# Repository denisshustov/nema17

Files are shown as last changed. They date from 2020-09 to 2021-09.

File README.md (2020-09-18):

# nema17

<b>#3_2.ino - arduino scatch for ultrasonic sensors</b><br>
<br>
links:
https://www.intorobotics.com/how-to-use-sensor_msgs-range-ros-for-multiple-sensors-with-rosserial/<br>
http://cobecoballes-robotics.blogspot.com/2018/08/sonar-ranger-ros-rviz.html<br>
http://wiki.ros.org/rosserial_arduino/Tutorials/SRF08%20Ultrasonic%20Range%20Finder<br>

if add Kalman filter it works slow<br>
if send in different topics it works slow<br>

<b>RUN</b><br>
rosrun rosserial_python serial_node.py /dev/ttyUSB0<br>
rostopic echo /rangeSonar1<br>

#ultrasonic sensors problems<br>
if error like:<br>
~$ roslaunch turtlebot3_bringup turtlebot3_robot.launch <br>
... logging to /home/turtlebot3/.ros/log/50d0066c-1356-11e8-861b-a0c589238c19/roslaunch-turtlebot3-2515.log<br>
Checking log directory for disk usage. This may take awhile.<br>
Press Ctrl-C to interrupt<br>
Done checking log file disk usage. Usage is <1GB.<br>
<br>
<br>
Solution:<br>
change arduino with more RAM or cut code for arduino<br>

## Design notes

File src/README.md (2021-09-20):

# Vacuum cleaner operation by ROS

## Model
For desing use Fusion 360. For converting from Fusion 360 to urfd tool: https://github.com/syuntoku14/fusion2urdf

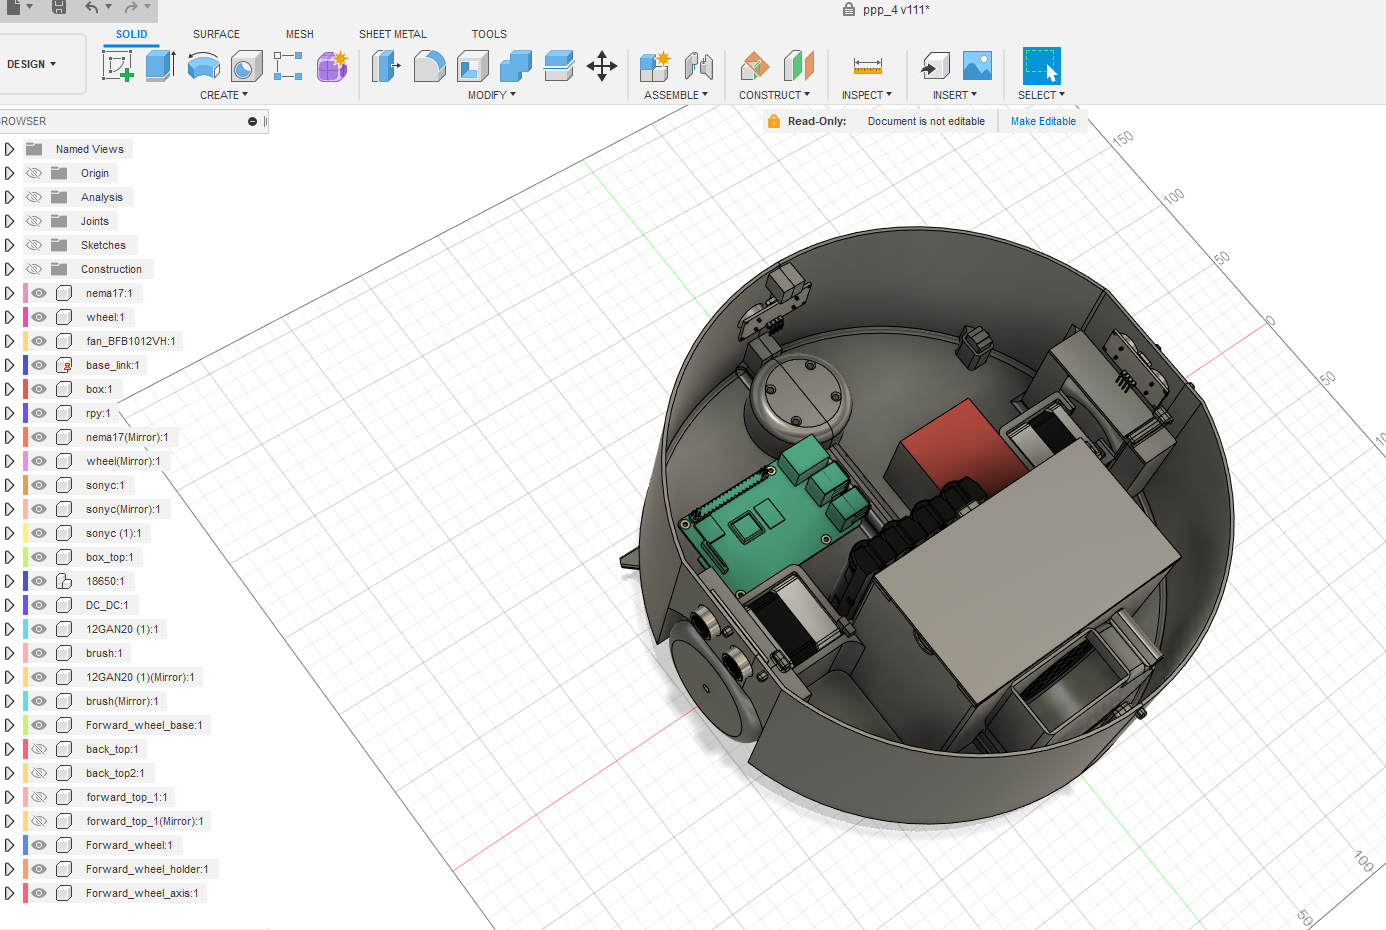
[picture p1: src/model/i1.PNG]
N|Solid


link to model f2d: [model/ppp_4_v79_c.f3d](model/ppp_4_v79_c.f3d)

## Details

1) Raspberry py 3<br>
2) Lidar rplidar a1<br>
3) Motor Nema17<br>
4) Two small motors with reductor for brushes like this (https://www.amazon.com/uxcell-36RPM-Reduction-Terminals-Engine/dp/B0716T8KPD)<br>
5) Driver DRV8825<br>
6) IMU - remove b/c it get a lot of diveation<br>
7) 18650x4<br>
8) UltraSonic sensors x 2

## Soft
For robot use Ubuntu 18, but it has some problems with wifi. And ROS melodic.
For PC use Ubuntu 20 and ROS noetic.

## Run
run launch file on raspberry<br>
```
ppp_run/launch/ppp_run.launch 
```
and run on PC it sepatate console:
```
roslaunch nav nav.launch 
roslaunch path_creator path_creator.launch 
roslaunch path_visualizer path_visualizer.launch 
roslaunch path_creator_goal_mover path_creator.launch
```

## Links

| Node | README |
| --- | --- |
| Brush UltraSonyc Sensors and Voltage | [brushUltraSonycSensorsVoltage](brushUltraSonycSensorsVoltage) |
| convert_range_sensors_values | [convert_range_sensors_values](convert_range_sensors_values) |
| motor_driver | [motor_driver](motor_driver) |
| odom_publisher | [odom_publisher](odom_publisher) |
| path_creator | [path_creator](path_creator) |

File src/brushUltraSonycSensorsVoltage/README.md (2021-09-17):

# brushUltraSonycSensorsVoltage

3_2.ino - arduino scatch for ultrasonic sensors and voltage measure to receive <br>
and subscribe funAndBrushes

rangeSonar is raw data for get normal data use convert_range_sensors_values [../convert_range_sensors_values/README.md](../convert_range_sensors_values/README.md)

# Topics
public:
rangeSonar1 - Float32MultiArray, it contains 3 values<br>
voltage - Float32

subscribe:
funAndBrushes - ByteMultiArray, it receive 3 values, for two brushes and one turbine

# RUN
rosrun rosserial_python serial_node.py /dev/ttyUSB0<br>

run funAndBrushes:<br>
```python
rostopic pub /funAndBrushes std_msgs/ByteMultiArray "layout:
  dim:
  - label: ''
    size: 3
    stride: 0
  data_offset: 0
data:
- 1
- 1
- 1" 
```
stop funAndBrushes:<br>
```python
rostopic pub /funAndBrushes std_msgs/ByteMultiArray "layout:
  dim:
  - label: ''
    size: 3
    stride: 0
  data_offset: 0
data:
- 0
- 0
- 0" 
```

see topic
rostopic echo /rangeSonar1<br>
rostopic echo /voltage<br>

# Circumstance
<b>if add Kalman filter it works slow</b><br>

<b>if send in different topics it works slow</b><br>

ultrasonic sensors problems<br>
if error like:<br>
~$ roslaunch turtlebot3_bringup turtlebot3_robot.launch <br>
... logging to /home/turtlebot3/.ros/log/50d0066c-1356-11e8-861b-a0c589238c19/roslaunch-turtlebot3-2515.log<br>
Checking log directory for disk usage. This may take awhile.<br>
Press Ctrl-C to interrupt<br>
Done checking log file disk usage. Usage is <1GB.<br>
<b>Solution:</b><br>
change arduino with more RAM or cut code for arduino<br>

# Links
https://www.intorobotics.com/how-to-use-sensor_msgs-range-ros-for-multiple-sensors-with-rosserial/<br>
http://cobecoballes-robotics.blogspot.com/2018/08/sonar-ranger-ros-rviz.html<br>
http://wiki.ros.org/rosserial_arduino/Tutorials/SRF08%20Ultrasonic%20Range%20Finder<br>

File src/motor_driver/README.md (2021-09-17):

# motor_driver

# Code 
motor_driver.py
motor-driver.launch

and launch in reapberry

# How it works
Subscribe topic /ppp/cmd_vel and translate it to velocity for eatch motor<br>
and publish topic /ppp/real_cmd_vel, b/c it can't make actually values that sended by cmd_vel<br>
It convert linear speed to rpm:

```python
l_vel = msg.linear.x - ((self.wheelSep / 2.0) * msg.angular.z)# m/s
r_vel = msg.linear.x + ((self.wheelSep / 2.0) * msg.angular.z)# m/s

self._left_rpm = l_vel / self.DIST_PER_RAD
self._right_rpm = r_vel / self.DIST_PER_RAD
```
wheelSep - distance between wheels<br>
DIST_PER_RAD - it distance per radian<br>

And in Motor_Driver.run receive rpm_left, rpm_right<br>
witch convert to frequency<br>

```python
fz_left = (rpm_left * 60) / 0.3
fz_right = (rpm_right * 60) / 0.3
```
this magic number get from https://www.se.com/no/en/faqs/FA337686/<br>
and run it.<br>
But it runs not with correct frequency. Correct frequency get by<br>

```python
real_fz_left = self.pi.get_PWM_frequency(self.STEP1)
real_fz_right = self.pi.get_PWM_frequency(self.STEP2)

real_fz_left = real_fz_left * math.copysign(1, fz_left)
real_fz_right = real_fz_right * math.copysign(1, fz_right)

real_rpm_left = (real_fz_left * 0.3) / 60
real_rpm_right = (real_fz_right * 0.3) / 60

real_velocity_left = real_rpm_left * self.DIST_PER_RAD
real_velocity_right = real_rpm_right * self.DIST_PER_RAD
```
and convert it to velocity

# Links
https://www.rototron.info/raspberry-pi-stepper-motor-tutorial/
https://www.se.com/no/en/faqs/FA337686/

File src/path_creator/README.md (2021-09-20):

# path_creator

# How to use
## path_creator_node 

Main service is [path_creator/src/path_creator_node.py](path_creator/src/path_creator_node.py)

it get map, split it to counturs, and generate path on eatch contur. Also you can merge counturs<br>
launch it:
```bash
roslaunch path_creator path_creator.launch 
```
<br>
in launch file you can merge it like this:<br>

```xml
<node name="path_creator" pkg="path_creator" output="screen" type="path_creator_node.py">
        <param name="merge_0" value="['0','1']" />
        <param name="merge_1" value="['2','3','4','5','6','7','8']" />
</node>
```

## path_visualizer

For visualize counturs and path

launch:
```
roslaunch path_visualizer path_visualizer.launch 
```

## path_creator_goal_mover
For start creating full covarage path of conurs, and run it by sending goals to move_base.
<br>
# Libs
Conturs.py - lib for work with counturs

ex.:
```python
cnt_inst = Conturs(image)
cnts = cnt_inst.get_conturs(40)
```
image like:<br>
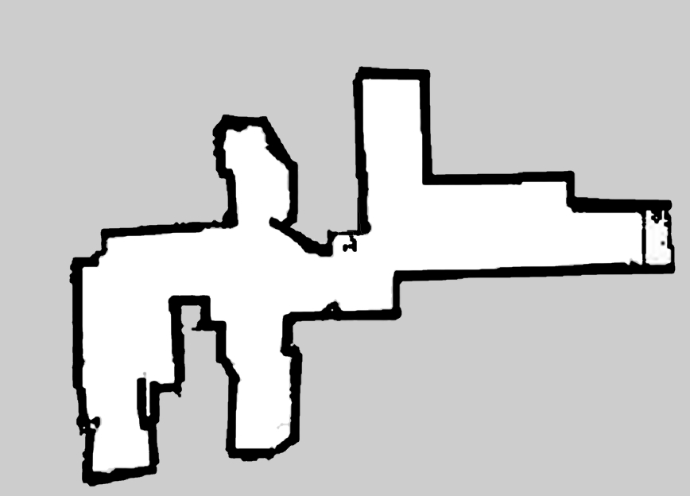
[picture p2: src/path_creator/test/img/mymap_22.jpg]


After get conturs:<br>
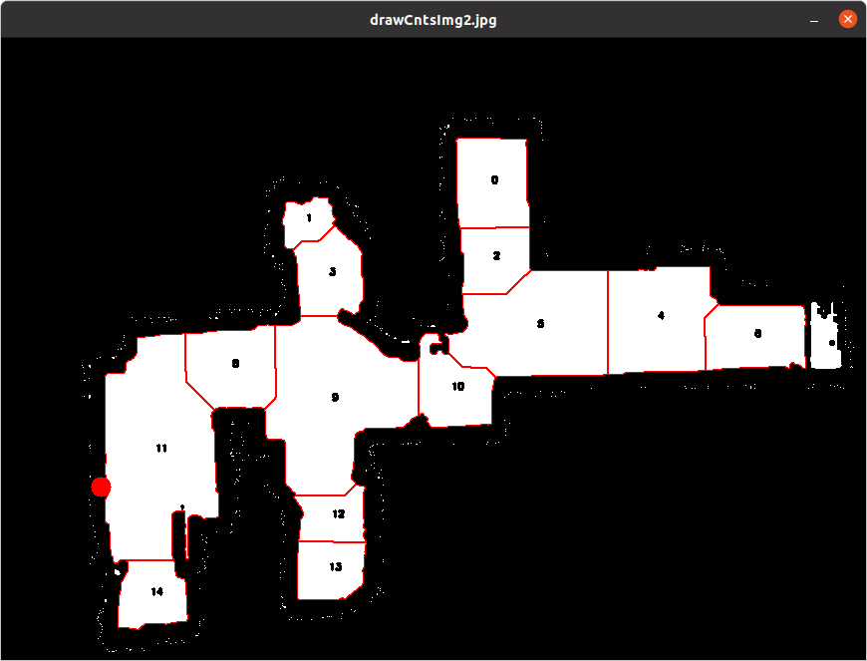
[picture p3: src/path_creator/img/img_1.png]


PathFinder.py - create path in the counturs

```python
pth = PathFinder(current_contur.contur, image.shape, 5, 1, start_point=start_point, debug_mode=True,neibor_distance=8)
covered_points = pth.get_route()
```

After get pathes:<br>
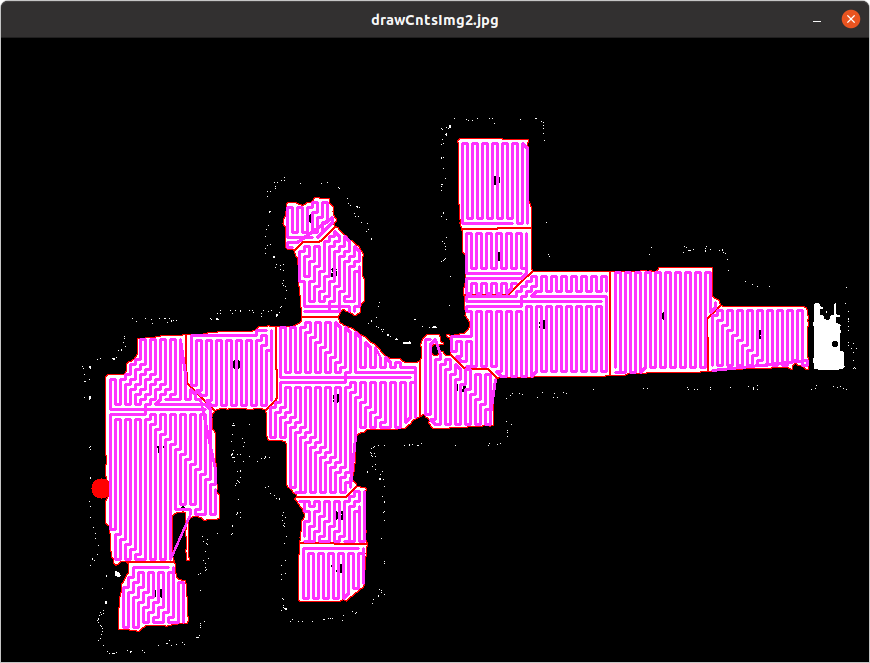
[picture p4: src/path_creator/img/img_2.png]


get_route is first version of path creation.

marker_lib.py - for markers in the map, like way points/line and goal indicator

# path_creator
path_creator_node.py - service<br>
subscribe /map topic<br>
call it:<br>
path_creator/get_by_id<br>
contur_creator/get_conturs<br>
contur_creator/get_by_id<br>
contur_creator/get_by_xy<br>
contur_creator/get_by_next_by_id<br>

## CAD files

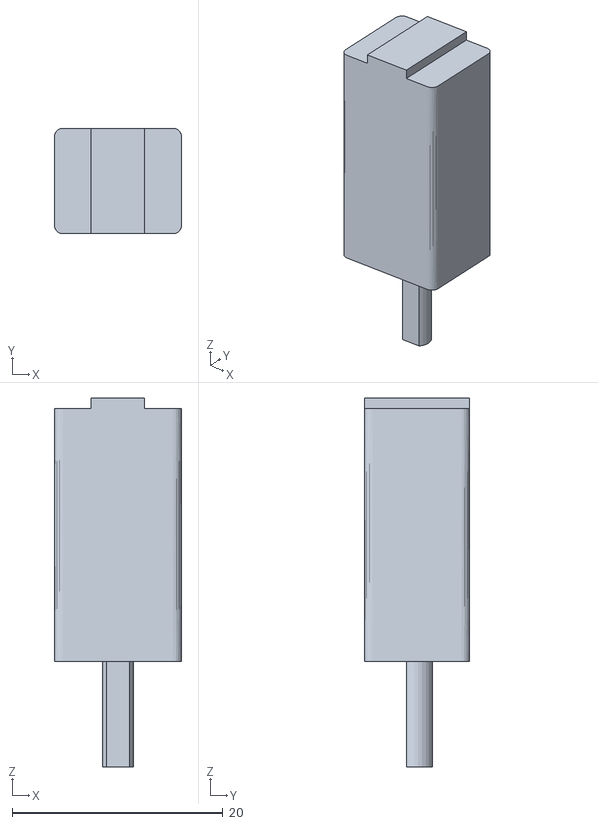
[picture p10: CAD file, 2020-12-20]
src/ppp90_description/meshes/12GAN20__1__1.stl
12.1 x 10.0 x 35.0

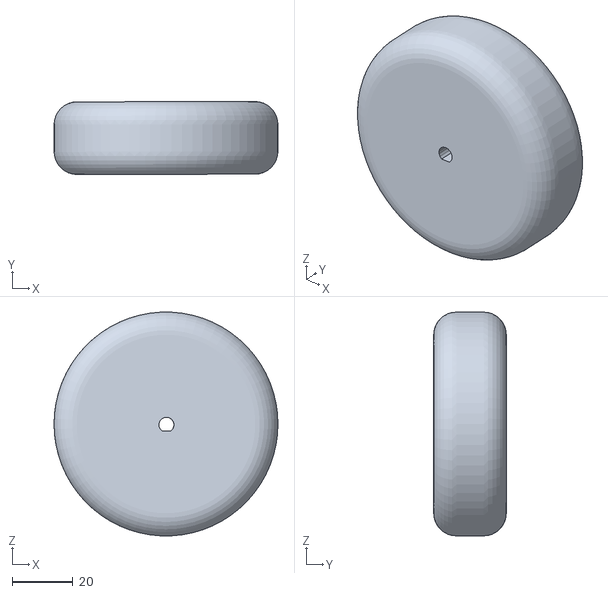
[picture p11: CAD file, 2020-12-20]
src/ppp90_description/meshes/wheel_Mirror__1.stl
74.0 x 24.1 x 73.9

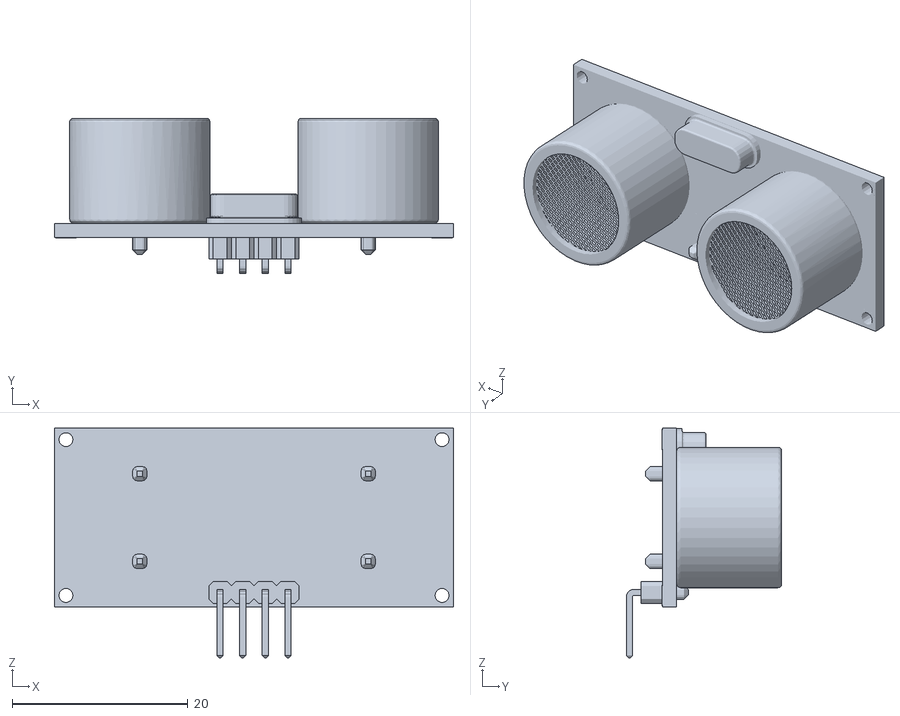
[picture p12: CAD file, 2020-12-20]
src/ppp90_description/meshes/sonyc_Mirror__1.stl
45.4 x 17.7 x 26.1

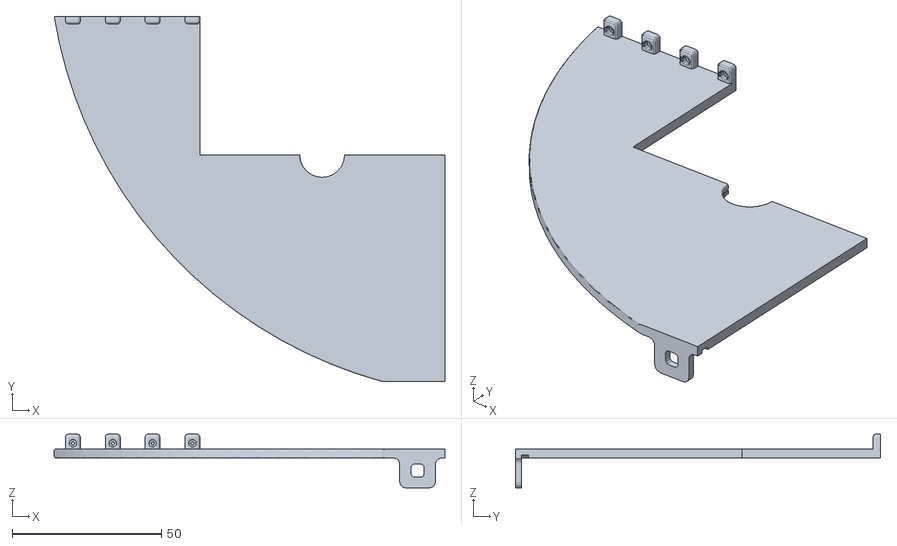
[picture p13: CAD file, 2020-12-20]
src/ppp90_description/meshes/back_top2_1.stl
130.8 x 122.2 x 18.0

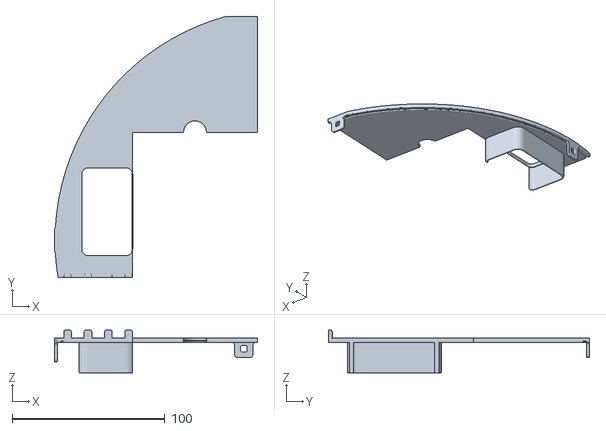
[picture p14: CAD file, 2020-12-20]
src/ppp90_description/meshes/back_top_1.stl
133.2 x 170.9 x 28.0

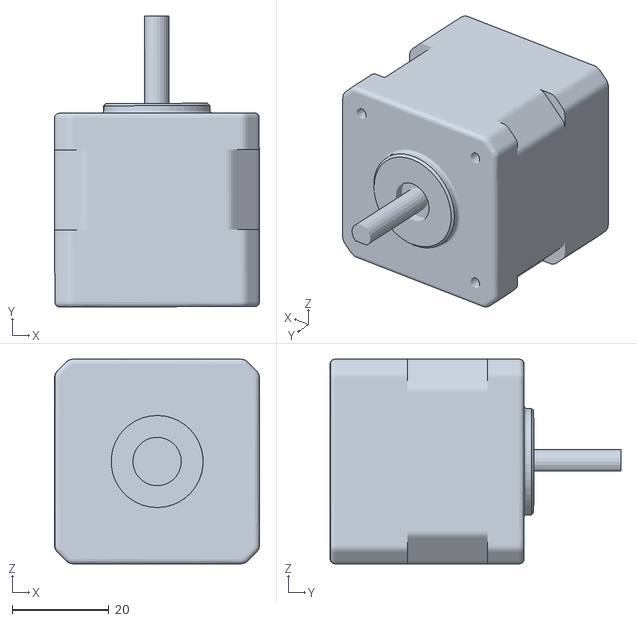
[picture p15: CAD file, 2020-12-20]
src/ppp90_description/meshes/nema17_Mirror__1.stl
42.3 x 60.0 x 42.2

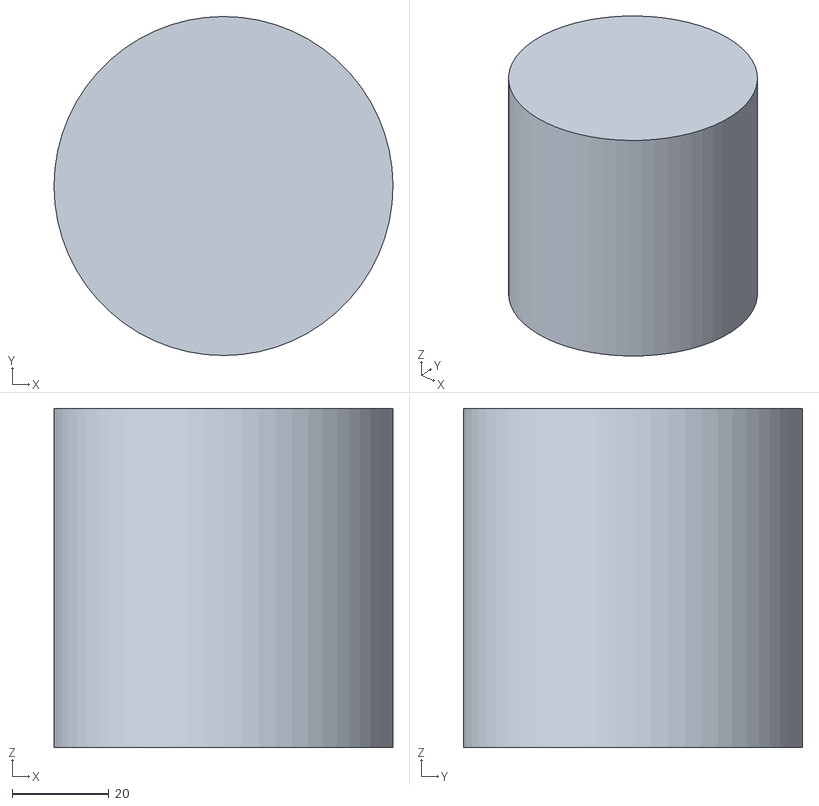
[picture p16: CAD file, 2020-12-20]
src/ppp90_description/meshes/Lidar_1.stl
70.0 x 70.0 x 70.0

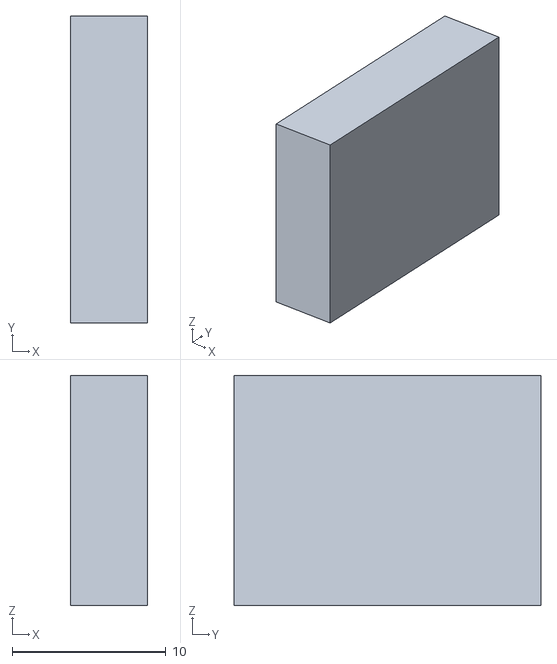
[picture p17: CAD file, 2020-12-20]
src/ppp90_description/meshes/IMU_1.stl
5.00 x 20.0 x 15.0

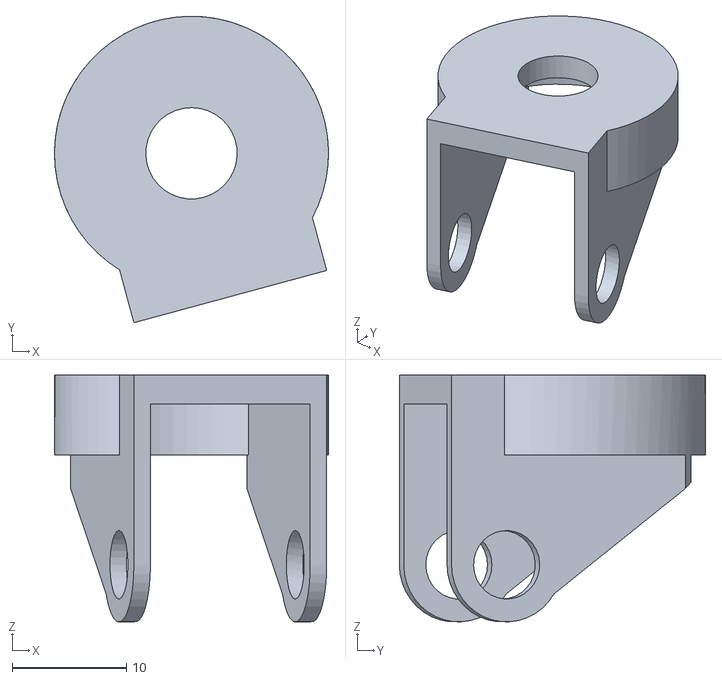
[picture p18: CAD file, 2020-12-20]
src/ppp90_description/meshes/Component35_1.stl
24.0 x 26.8 x 21.6

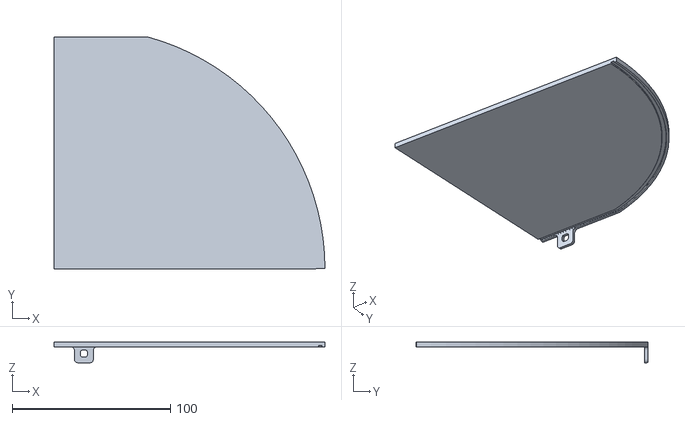
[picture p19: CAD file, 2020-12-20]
src/ppp90_description/meshes/forward_top_1_Mirror__1.stl
171.4 x 146.6 x 13.0

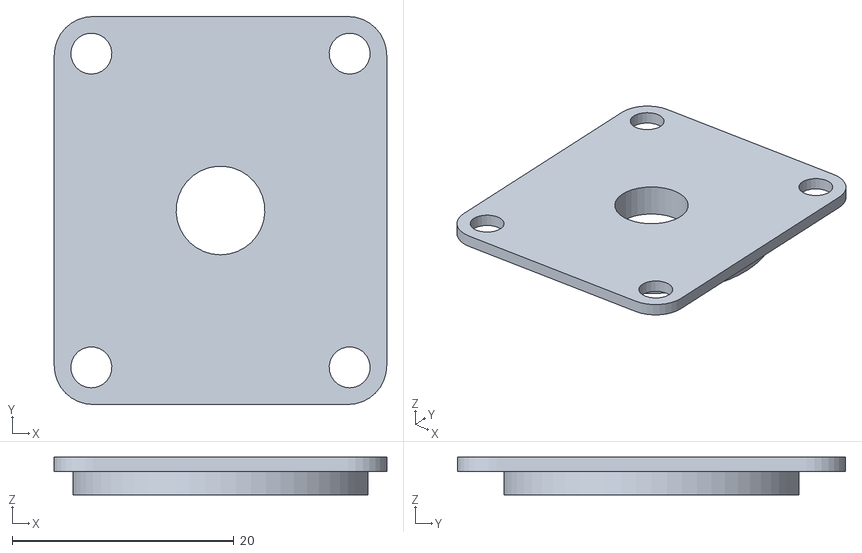
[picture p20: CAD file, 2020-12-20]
src/ppp90_description/meshes/Forward_wheel_1.stl
30.0 x 35.0 x 3.40

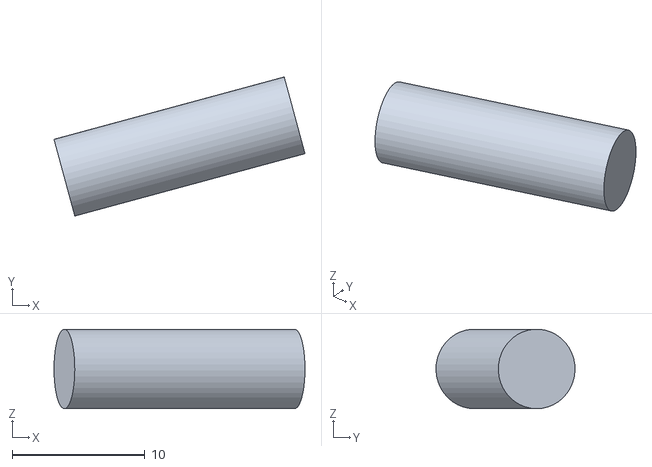
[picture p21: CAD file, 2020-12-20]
src/ppp90_description/meshes/Component37_1.stl
18.9 x 10.5 x 5.99

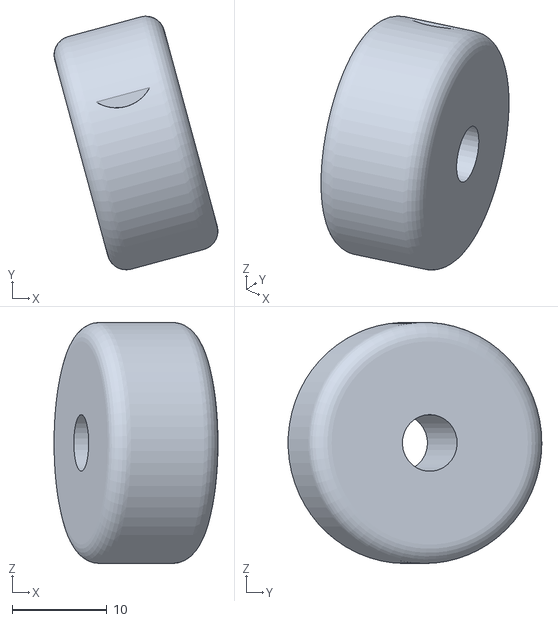
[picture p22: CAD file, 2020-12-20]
src/ppp90_description/meshes/Component36_1.stl
17.3 x 26.8 x 25.5

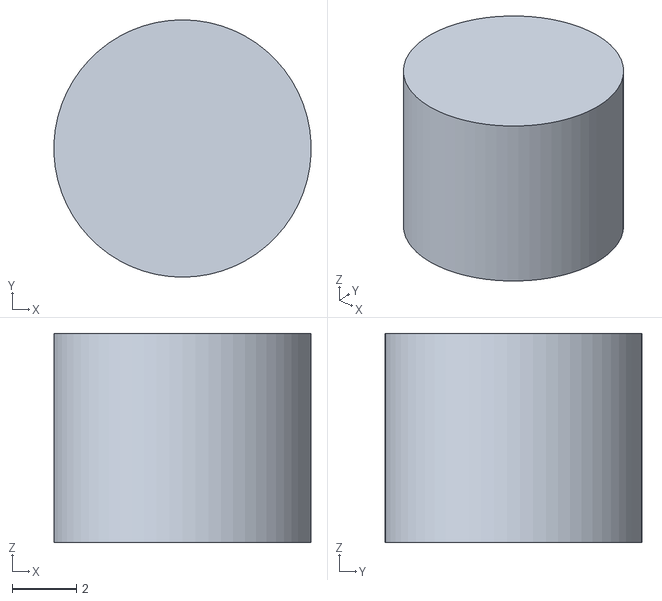
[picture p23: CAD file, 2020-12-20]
src/ppp90_description/meshes/Component38_1.stl
7.99 x 8.00 x 6.50

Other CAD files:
src/ppp90_description/meshes/sonyc_1.stl
src/ppp90_description/meshes/12GAN20__1__Mirror__1.stl
src/ppp90_description/meshes/forward_top_1_1.stl
src/ppp90_description/meshes/nema17_1.stl
src/ppp90_description/meshes/18650 (1) (1).stl
src/ppp90_description/meshes/18650 (1).stl
src/ppp90_description/meshes/18650 (2).stl
src/ppp90_description/meshes/Battery Holder v1 (1) (1).stl
src/ppp90_description/meshes/Battery Holder v1 (1).stl
src/ppp90_description/meshes/Battery Holder v1 (2).stl
src/ppp90_description/meshes/Battery Holder v1.stl
src/ppp90_description/meshes/DC_DC_1.stl
src/ppp90_description/meshes/Forward_wheel.stl
src/ppp90_description/meshes/base_link.stl
src/ppp90_description/meshes/box_1.stl
src/ppp90_description/meshes/box_top_1.stl
src/ppp90_description/meshes/brush_1.stl
src/ppp90_description/meshes/brush_Mirror__1.stl
src/ppp90_description/meshes/fw_wheel_1.stl
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

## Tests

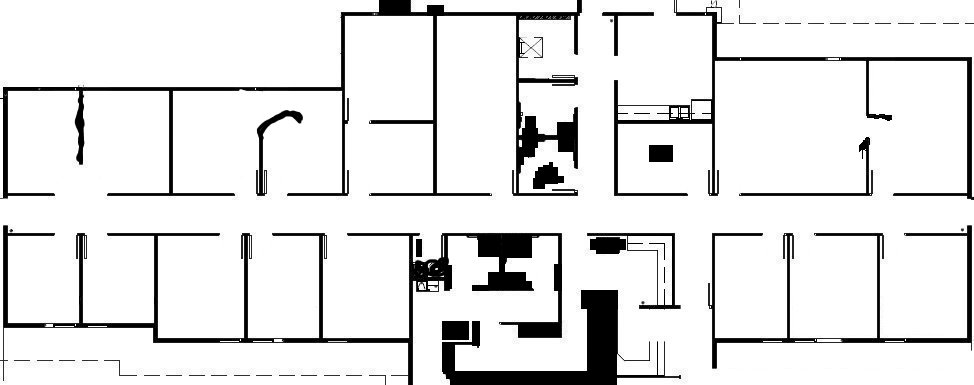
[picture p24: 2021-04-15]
src/path_creator/test/img/map.jpg

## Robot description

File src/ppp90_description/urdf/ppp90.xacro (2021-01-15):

<?xml version="1.0" ?>
<robot name="ppp90" xmlns:xacro="http://www.ros.org/wiki/xacro">

<xacro:include filename="$(find ppp90_description)/urdf/materials.xacro" />
<xacro:include filename="$(find ppp90_description)/urdf/ppp90.trans" />
<xacro:include filename="$(find ppp90_description)/urdf/ppp90.gazebo" />

<link name="base_footprint"/>

<joint name="base_joint" type="fixed">
    <parent link="base_footprint"/>
    <child link="base_link"/>
    <origin xyz="0.0 0.0 0.010" rpy="0 0 0"/>
</joint>

<link name="base_link">
  <inertial>
    <origin rpy="0 0 0" xyz="0 0 0"/>
    <mass value="5.029311101542255"/>
    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
  </inertial>
  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
</link>


<link name="roll_celinder">
    <inertial>
      <origin xyz="0 0 0" rpy="0 0 0"/>
      <mass value="0.1"/>
      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
    </inertial>
    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
</link>

<joint name="celinder_celinder" type="continuous">
  <origin xyz="0.12116 -0.014724 -0.001" rpy="0 0 0"/>
  <parent link="base_link"/>
  <child link="roll_celinder"/>
  <axis xyz="-0 -0.0 -1.0"/>
</joint>


<link name="ball">
  <inertial>
    <origin xyz="0 0 0" rpy="0 0 0"/>
    <mass value="4"/>
    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
  </inertial>
  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
</link>


<joint name="b_ball" type="continuous">
  <origin xyz="0.0 -0.0 -0.001" rpy="0 0 0"/>
  <parent link="roll_celinder"/>
  <child link="ball"/>
  <axis xyz="0.0 -1.0 -0.0"/>
</joint>

  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

<link name="wheel_1">
  <inertial>
    <origin rpy="0 0 0" xyz="6.395377760427118e-05 0.012000086928228931 -0.0002917507270338848"/>
    <mass value="0.7647072407364309"/>
    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
  </inertial>
  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
</link>

<link name="wheel_Mirror__1">
  <inertial>
    <origin rpy="0 0 0" xyz="-0.00015092559014278847 0.01200013936071219 0.0002680720190440314"/>
    <mass value="0.7647072407364308"/>
    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
  </inertial>
  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
</link>

<link name="sonyc_1">
  <inertial>
    <origin rpy="0 0 0" xyz="-0.012999900847315296 0.010235790299775449 5.063181308696818e-05"/>
    <mass value="0.0252883585593009"/>
    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
  </inertial>
  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
</link>

<link name="sonyc_Mirror__1">
  <inertial>
    <origin rpy="0 0 0" xyz="0.013000099152684503 -0.010236050318673445 5.063181308696818e-05"/>
    <mass value="0.025288358559300887"/>
    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
  </inertial>
  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
</link>

<link name="sonyc__1__1">
  <inertial>
    <origin rpy="0 0 0" xyz="-0.010235983367435975 0.012999694386711707 5.06318130869543e-05"/>
    <mass value="0.0252883585593009"/>
    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
  </inertial>
  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
</link>

<link name="nema17_1">
  <inertial>
    <origin rpy="0 0 0" xyz="1.1356221513089682e-06 0.0033428571345282126 0.021180135259303026"/>
    <mass value="0.1838412954712099"/>
    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
  </inertial>
  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
</link>

<link name="nema17_Mirror__1">
  <inertial>
    <origin rpy="0 0 0" xyz="6.439713466371497e-06 -0.003342366804660879 0.021180135259303026"/>
    <mass value="0.1838412954712099"/>
    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
  </inertial>
  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
</link>

<link name="12GAN20__1__1">
  <inertial>
    <origin rpy="0 0 0" xyz="-5.679885005938079e-07 2.662622002880255e-06 0.011857871337072685"/>
    <mass value="0.023492103087793172"/>
    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
  </inertial>
  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
</link>

<link name="brush_1">
  <inertial>
    <origin rpy="0 0 0" xyz="1.2765746805476486e-07 1.4332153454310603e-07 -0.0022204199308318365"/>
    <mass value="0.014937067448072668"/>
    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
  </inertial>
  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
</link>

<link name="brush_Mirror__1">
  <inertial>
    <origin rpy="0 0 0" xyz="-1.1351642089096892e-06 -6.856742623684298e-08 -0.0022204199308317827"/>
    <mass value="0.014937067448072664"/>
    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
  </inertial>
  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
</link>

<link name="12GAN20__1__Mirror__1">
  <inertial>
    <origin rpy="0 0 0" xyz="-2.596503974161557e-06 6.725409899849266e-06 0.011857871337072688"/>
    <mass value="0.02349210308779317"/>
    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
  </inertial>
  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
</link>

<link name="forward_top_1_1">
  <inertial>
    <origin rpy="0 0 0" xyz="-0.09472371095209488 -0.06502162145818441 0.0004895173930853369"/>
    <mass value="0.48710215659029577"/>
    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
  </inertial>
  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
</link>

<link name="forward_top_1_Mirror__1">
  <inertial>
    <origin rpy="0 0 0" xyz="0.0735909092846742 -0.07845842785085694 0.0004895171912021601"/>
    <mass value="0.48710223650351714"/>
    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
  </inertial>
  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
</link>

<link name="back_top_1">
  <inertial>
    <origin rpy="0 0 0" xyz="-0.06983924477939416 -0.07365384534784823 -0.0010887199497685157"/>
    <mass value="0.23560428740017997"/>
    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
  </inertial>
  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
</link>

<link name="back_top2_1">
  <inertial>
    <origin rpy="0 0 0" xyz="-0.05870936689603044 0.05499707718659973 0.0004968868769272966"/>
    <mass value="0.18961170684744505"/>
    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
  </inertial>
  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
</link>

<link name="Lidar_Box">
  <inertial>
    <origin rpy="0 0 0" xyz="3.0855486037040247e-07 2.620424081334338e-07 0.03500000000000002"/>
    <mass value="2.114723824855799"/>
    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
  </inertial>
  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
</link>

<link name="Lidar_1">
  <inertial>
    <origin rpy="0 0 0" xyz="0 0 0"/>
    <mass value="0.001"/>
    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
  </inertial>
  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
</link>

<joint name="Lidar_box_to_base_link" type="fixed">
  <origin rpy="0 0 0" xyz="0.115679 -0.143452 0.002"/>
  <parent link="forward_top_1_Mirror__1"/>
  <child link="Lidar_Box"/>
</joint>


<joint name="Lidar_Box_LIDAR" type="fixed">
  <origin rpy="0 0 3.14159" xyz="0.0 0 0.07"/>
  <parent link="Lidar_Box"/>
  <child link="Lidar_1"/>
  <axis xyz="0.0 -1.0 -0.0"/>
</joint>

<link name="base_imu_link">
  <inertial>
    <origin rpy="0 0 0" xyz="-0.158919 0.014494 -0.033"/>
    <mass value="0.011774999999999999"/>
    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
  </inertial>
  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
</link>


<joint name="Rev1" type="continuous">
  <origin rpy="3.14159 0 0" xyz="0.0 -0.025 0.021125"/>
  <parent link="nema17_1"/>
  <child link="wheel_1"/>
  <axis xyz="0.0 -1.0 -0.0"/>
</joint>

<joint name="Rev4" type="continuous">
  <origin rpy="0 0 0" xyz="-3.7e-05 0.02285 0.021125"/>
  <parent link="nema17_Mirror__1"/>
  <child link="wheel_Mirror__1"/>
  <axis xyz="-0.001615 0.999999 0.0"/>
</joint>

<joint name="Rigid5" type="fixed">
  <origin rpy="0 0 -1.5708" xyz="0.027338 -0.165062 0.08983"/>
  <parent link="base_link"/>
  <child link="sonyc_1"/>
</joint>

<joint name="Rigid6" type="fixed">
  <origin rpy="0 0 1.5708" xyz="0.001338 0.136075 0.08983"/>
  <parent link="base_link"/>
  <child link="sonyc_Mirror__1"/>
</joint>

<joint name="Rigid7" type="fixed">
  <origin rpy="0 0 0" xyz="0.169259 -0.02747 0.06983"/>
  <parent link="base_link"/>
  <child link="sonyc__1__1"/>
</joint>

<joint name="Rigid8" type="fixed">
  <origin rpy="0 0 0" xyz="0.014338 -0.112903 0.003"/>
  <parent link="base_link"/>
  <child link="nema17_1"/>
</joint>

<joint name="Rigid9" type="fixed">
  <origin rpy="0 0 0" xyz="0.014372 0.084506 0.003"/>
  <parent link="base_link"/>
  <child link="nema17_Mirror__1"/>
</joint>

<joint name="Rigid13" type="fixed">
  <origin rpy="0 0 0" xyz="0.096298 0.098909 0.001"/>
  <parent link="base_link"/>
  <child link="12GAN20__1__1"/>
</joint>

<joint name="Rev14" type="continuous">
  <origin rpy="0 0 0" xyz="2e-06 1e-05 -0.002"/>
  <parent link="12GAN20__1__1"/>
  <child link="brush_1"/>
  <axis xyz="0.0 -0.0 -1.0"/>
</joint>

<joint name="Rev15" type="continuous">
  <origin rpy="0 0 0" xyz="0.0 0.0 -0.002"/>
  <parent link="12GAN20__1__Mirror__1"/>
  <child link="brush_Mirror__1"/>
  <axis xyz="-0.0 0.0 -1.0"/>
</joint>

<joint name="Rigid16" type="fixed">
  <origin rpy="0 0 0" xyz="0.096296 -0.127886 0.001"/>
  <parent link="base_link"/>
  <child link="12GAN20__1__Mirror__1"/>
</joint>

<joint name="Rigid21" type="fixed">
  <origin rpy="0 0 0" xyz="0.163338 -0.014494 0.11"/>
  <parent link="base_link"/>
  <child link="forward_top_1_1"/>
</joint>

<joint name="Rigid22" type="fixed">
  <origin rpy="0 0 0" xyz="-0.005021 0.129037 0.11"/>
  <parent link="base_link"/>
  <child link="forward_top_1_Mirror__1"/>
</joint>

<joint name="Rigid23" type="fixed">
  <origin rpy="0 0 0" xyz="-0.005021 0.129037 0.11"/>
  <parent link="base_link"/>
  <child link="back_top_1"/>
</joint>

<joint name="Rigid24" type="fixed">
  <origin rpy="0 0 0" xyz="-0.005021 -0.158024 0.11"/>
  <parent link="base_link"/>
  <child link="back_top2_1"/>
</joint>
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

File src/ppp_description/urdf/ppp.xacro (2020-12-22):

<?xml version="1.0" ?>
<robot name="ppp" xmlns:xacro="http://www.ros.org/wiki/xacro">

<xacro:include filename="$(find ppp_description)/urdf/materials.xacro" />
<xacro:include filename="$(find ppp_description)/urdf/ppp.trans" />
<xacro:include filename="$(find ppp_description)/urdf/ppp.gazebo" />

<link name="base_footprint"/>

<joint name="base_joint" type="fixed">
    <parent link="base_footprint"/>
    <child link="base_link"/>
    <origin xyz="0.0 0.0 0.010" rpy="0 0 0"/>
</joint>

<link name="base_link">
  <inertial>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
    <origin rpy="0 0 0" xyz="1.5201671826907086e-05 -0.0012107786655712151 0.03300924453524418"/>
    <mass value="4.737374361291242"/>
    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
  </inertial>
  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
</link>

<link name="wheel_1">
  <inertial>
    <origin rpy="0 0 0" xyz="-0.01199971693767804 6.38590668516137e-05 -0.0002917507270338848"/>
    <mass value="0.7647072407364309"/>
    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
  </inertial>
  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
</link>

<link name="wheel_Mirror__1">
  <inertial>
    <origin rpy="0 0 0" xyz="-0.011999769370161381 -0.00015102030089534307 0.00026807201904404526"/>
    <mass value="0.7647072407364308"/>
    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
  </inertial>
  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
</link>

<link name="sonyc_1">
  <inertial>
    <origin rpy="0 0 0" xyz="-0.010235420309224613 -0.012999995558067955 5.063181308696818e-05"/>
    <mass value="0.0252883585593009"/>
    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
  </inertial>
  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
</link>

<link name="sonyc_Mirror__1">
  <inertial>
    <origin rpy="0 0 0" xyz="0.010235420309224252 0.01300000444193195 5.063181308696818e-05"/>
    <mass value="0.025288358559300887"/>
    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
  </inertial>
  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
</link>

<link name="sonyc__1__1">
  <inertial>
    <origin rpy="0 0 0" xyz="-0.01300032439616085 -0.010236078078188549 5.06318130869543e-05"/>
    <mass value="0.0252883585593009"/>
    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
  </inertial>
  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
</link>

<link name="nema17_1">
  <inertial>
    <origin rpy="0 0 0" xyz="-0.003342487143977363 1.0409113986613717e-06 0.02118013525930302"/>
    <mass value="0.1838412954712099"/>
    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
  </inertial>
  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
</link>

<link name="nema17_Mirror__1">
  <inertial>
    <origin rpy="0 0 0" xyz="0.0033427367952116732 6.3450027137950304e-06 0.021180135259303026"/>
    <mass value="0.1838412954712099"/>
    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
  </inertial>
  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
</link>

<link name="12GAN20__1__1">
  <inertial>
    <origin rpy="0 0 0" xyz="-3.292631452073147e-06 -6.626992531399978e-07 0.01185787133707267"/>
    <mass value="0.023492103087793172"/>
    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
  </inertial>
  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
</link>

<link name="brush_1">
  <inertial>
    <origin rpy="0 0 0" xyz="-7.733309837359981e-07 3.2946715564086126e-08 -0.0022204199308318265"/>
    <mass value="0.014937067448072668"/>
    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
  </inertial>
  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
</link>

<link name="brush_Mirror__1">
  <inertial>
    <origin rpy="0 0 0" xyz="-5.614420229005379e-07 -1.2298749614975124e-06 -0.0022204199308317844"/>
    <mass value="0.014937067448072664"/>
    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
  </inertial>
  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
</link>

<link name="12GAN20__1__Mirror__1">
  <inertial>
    <origin rpy="0 0 0" xyz="-7.3554193489588915e-06 -2.6912147267910136e-06 0.011857871337072678"/>
    <mass value="0.02349210308779317"/>
    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
  </inertial>
  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
</link>
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
<link name="FW_baise_1">
  <inertial>
    <origin rpy="0 0 0" xyz="0.014149999999964021 -0.011650110353972745 -0.0014374507094137914"/>
    <mass value="0.0061871055650105375"/>
    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
  </inertial>
  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
</link>

<link name="wheel__1__1">
  <inertial>
    <origin rpy="0 0 0" xyz="1.872807464664561e-14 -1.1035397273762015e-07 4.466912950640278e-17"/>
    <mass value="0.0030771108424005812"/>
    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
  </inertial>
  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
</link>

<link name="axis_1">
  <inertial>
    <origin rpy="0 0 0" xyz="0.03303899999968629 -1.1035397272374237e-07 -0.035509999999999944"/>
    <mass value="0.0043107049436968805"/>
    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
  </inertial>
  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
</link>

<link name="holder_1">
  <inertial>
    <origin rpy="0 0 0" xyz="0.0011550098836461376 -3.867842181329295e-06 -0.0024145150891157104"/>
    <mass value="0.006489971019909515"/>
    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
  </inertial>
  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
</link>
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

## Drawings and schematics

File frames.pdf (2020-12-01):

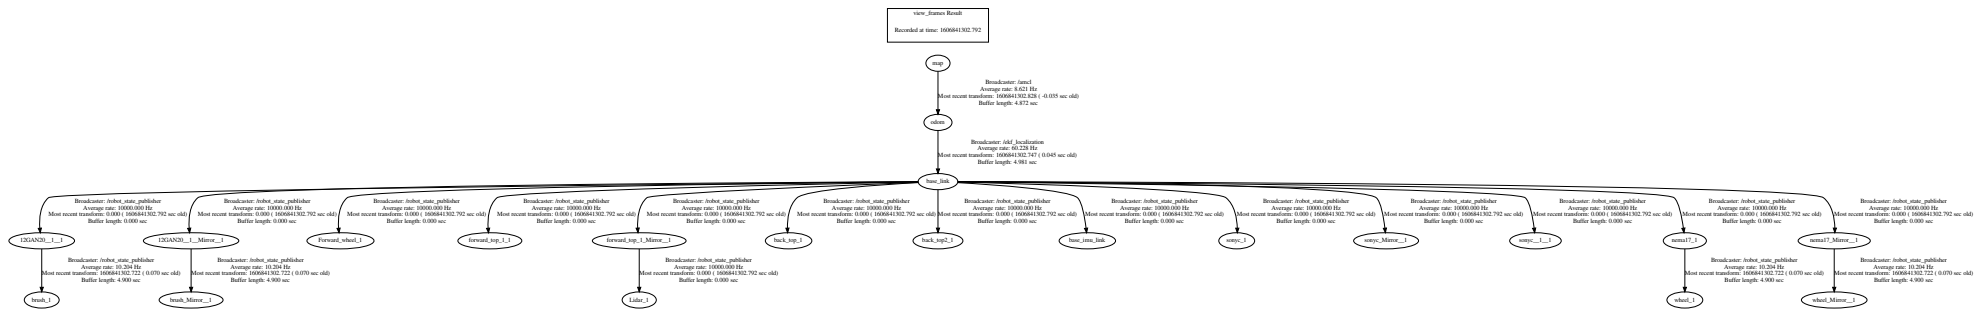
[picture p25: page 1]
view_frames Result; base_link; 12GAN20__1__1; 12GAN20__1__Mirror__1; Forward_wheel_1; forward_top_1_1; forward_top_1_Mirror__1; back_top_1; back_top2_1; base_imu_link; sonyc_1; sonyc_Mirror__1; sonyc__1__1; nema17_1; nema17_Mirror__1; brush_1; odom; brush_Mirror__1; Lidar_1; wheel_1; wheel_Mirror__1; map

Recorded at time: 1606841302.792

Broadcaster: /amcl
Average rate: 8.621 Hz
Buffer length: 4.872 sec

Most recent transform: 1606841302.828 ( -0.035 sec old)

Broadcaster: /ekf_localization
Average rate: 60.228 Hz
Buffer length: 4.981 sec

Most recent transform: 1606841302.747 ( 0.045 sec old)

Broadcaster: /robot_state_publisher
Average rate: 10000.000 Hz
Buffer length: 0.000 sec

Most recent transform: 0.000 ( 1606841302.792 sec old)

Average rate: 10.204 Hz
Buffer length: 4.900 sec

Most recent transform: 1606841302.722 ( 0.070 sec old)

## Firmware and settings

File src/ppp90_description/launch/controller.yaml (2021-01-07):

# Publish all joint states -----------------------------------
joint_state_controller:
  type: joint_state_controller/JointStateController
  publish_rate: 50

# Position Controllers --------------------------------------
# Rev1_position_controller:
#   type: velocity_controllers/JointVelocityController
#   joint: Rev1
# Rev4_position_controller:
#   type: velocity_controllers/JointVelocityController
#   joint: Rev4

# gazebo_ros_control:
#   pid_gains:
#     Rev1:
#       {p: 0.00015, i: 0, d: 0}
#     Rev4:
#       {p: 0.00015, i: 0, d: 0}

# Differential Drive Controller --------------------------------------
diff_drive_controller:
  type: "diff_drive_controller/DiffDriveController"
  left_wheel: 'Rev1'
  right_wheel: 'Rev4'
  wheel_separation : 0.24
  wheel_radius : 0.037
  cmd_vel_timeout: 0.25
  publish_rate: 20.0
  base_frame_id: base_footprint
  # # Base frame_id
  # base_frame_id: base_footprint #default: base_link
  # pose_covariance_diagonal : [0.001, 0.001, 1000000.0, 1000000.0, 1000000.0, 1000.0]
  # twist_covariance_diagonal: [0.001, 0.001, 1000000.0, 1000000.0, 1000000.0, 1000.0]

  # Velocity and acceleration limits
  # Whenever a min_* is unspecified, default to -max_*
  # linear:
  #   x:
  #     has_velocity_limits    : true
  #     max_velocity           : 1.0  # m/s
  #     min_velocity           : -0.5 # m/s
  #     has_acceleration_limits: true
  #     max_acceleration       : 0.8  # m/s^2
  #     min_acceleration       : -0.4 # m/s^2
  #     has_jerk_limits        : true
  #     max_jerk               : 5.0  # m/s^3
  # angular:
  #   z:
  #     has_velocity_limits    : true
  #     max_velocity           : 1.7  # rad/s
  #     has_acceleration_limits: true
  #     max_acceleration       : 1.5  # rad/s^2
  #     has_jerk_limits        : true
  #     max_jerk               : 2.5  # rad/s^3

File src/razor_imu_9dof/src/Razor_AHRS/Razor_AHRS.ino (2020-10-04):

/***************************************************************************************************************
* Razor AHRS Firmware
* 9 Degree of Measurement Attitude and Heading Reference System
* for Sparkfun "9DOF Razor IMU" (SEN-10125 and SEN-10736)
* and "9DOF Sensor Stick" (SEN-10183, 10321 and SEN-10724)
*
* Released under GNU GPL (General Public License) v3.0
* Copyright (C) 2013 Peter Bartz [http://ptrbrtz.net]
* Copyright (C) 2011-2012 Quality & Usability Lab, Deutsche Telekom Laboratories, TU Berlin
*
* Infos, updates, bug reports, contributions and feedback:
*     https://github.com/ptrbrtz/razor-9dof-ahrs
*
*
* History:
*   * Original code (http://code.google.com/p/sf9domahrs/) by Doug Weibel and Jose Julio,
*     based on ArduIMU v1.5 by Jordi Munoz and William Premerlani, Jose Julio and Doug Weibel. Thank you!
*
*   * Updated code (http://groups.google.com/group/sf_9dof_ahrs_update) by David Malik (david.zsolt.malik@gmail.com)
*     for new Sparkfun 9DOF Razor hardware (SEN-10125).
*
*   * Updated and extended by Peter Bartz (peter-bartz@gmx.de):
*     * v1.3.0
*       * Cleaned up, streamlined and restructured most of the code to make it more comprehensible.
*       * Added sensor calibration (improves precision and responsiveness a lot!).
*       * Added binary yaw/pitch/roll output.
*       * Added basic serial command interface to set output modes/calibrate sensors/synch stream/etc.
*       * Added support to synch automatically when using Rovering Networks Bluetooth modules (and compatible).
*       * Wrote new easier to use test program (using Processing).
*       * Added support for new version of "9DOF Razor IMU": SEN-10736.
*       --> The output of this code is not compatible with the older versions!
*       --> A Processing sketch to test the tracker is available.
*     * v1.3.1
*       * Initializing rotation matrix based on start-up sensor readings -> orientation OK right away.
*       * Adjusted gyro low-pass filter and output rate settings.
*     * v1.3.2
*       * Adapted code to work with new Arduino 1.0 (and older versions still).
*     * v1.3.3
*       * Improved synching.
*     * v1.4.0
*       * Added support for SparkFun "9DOF Sensor Stick" (versions SEN-10183, SEN-10321 and SEN-10724).
*     * v1.4.1
*       * Added output modes to read raw and/or calibrated sensor data in text or binary format.
*       * Added static magnetometer soft iron distortion compensation.
*     * v1.4.2
*       * (No core firmware changes)
*     * v1.5
*       * Added support for "9DoF Razor IMU M0": SEN-14001.
*     * v1.5.1
*       * Added ROS-compatible output mode.
*     * v1.5.2
*       * Added ROS-compatible input mode to set calibration parameters.
*     * v1.5.3
*       * Fixed the problem where commands were ignored by the M0 depending on how they were sent.
*     * v1.5.4
*       * Attempts to fix random nan problems in orientation computations.
*       * Added an option to get yaw/pitch/roll from the M0 DMP.
*       * Added a command to enable/disable the use of magnetometers for yaw computation.
*     * v1.5.5
*       * Added various options to determine the most stable configuration for the M0.
*     * v1.5.6
*       * Removed some unnecessary math error checking.
*       * Set back gyro full-scale range to the maximum for the M0.
*       * Increased startup delay to try to get a correct initial orientation for the M0.
*     * v1.5.7
*       * Calibration data are now also used to compute the initial orientation.
*
* TODOs:
*   * Allow optional use of Flash/EEPROM for storing and reading calibration values.
*   * Use self-test and temperature-compensation features of the sensors.
***************************************************************************************************************/

/*
  "9DoF Razor IMU M0" hardware versions: SEN-14001

  Arduino IDE : Follow the same instructions as for the default firmware on 
  https://learn.sparkfun.com/tutorials/9dof-razor-imu-m0-hookup-guide 
  and use an updated version of SparkFun_MPU-9250-DMP_Arduino_Library from 
  https://github.com/lebarsfa/SparkFun_MPU-9250-DMP_Arduino_Library"
*/

/*
  "9DOF Razor IMU" hardware versions: SEN-10125 and SEN-10736

  ATMega328@3.3V, 8MHz

  ADXL345  : Accelerometer
  HMC5843  : Magnetometer on SEN-10125
  HMC5883L : Magnetometer on SEN-10736
  ITG-3200 : Gyro

  Arduino IDE : Select board "Arduino Pro or Pro Mini (3.3v, 8Mhz) w/ATmega328"
*/

/*
  "9DOF Sensor Stick" hardware versions: SEN-10183, SEN-10321 and SEN-10724

  ADXL345  : Accelerometer
  HMC5843  : Magnetometer on SEN-10183 and SEN-10321
  HMC5883L : Magnetometer on SEN-10724
  ITG-3200 : Gyro
*/

/*
  Axis definition (differs from definition printed on the board!):
    X axis pointing forward (towards the short edge with the connector holes)
    Y axis pointing to the right
    and Z axis pointing down.
    
  Positive yaw   : clockwise
  Positive roll  : right wing down
  Positive pitch : nose up
  
  Transformation order: first yaw then pitch then roll.
*/

/*
  Serial commands that the firmware understands:
  
  "#c<params>" - SET _c_alibration parameters. The available options are:
    [a|m|g|c|t] _a_ccelerometer, _m_agnetometer, _g_yro, magnetometerellipsoid_c_enter, magnetometerellipsoid_t_ransform.
    [x|y|z] x,y or z.
    [m|M|X|Y|Z] _m_in or _M_ax (accel or magnetometer), X, Y, or Z of transform (magnetometerellipsoid_t_ransform).


  "#p" - PRINT current calibration values.


  "#o<params>" - Set OUTPUT mode and parameters. The available options are:
  
      // Streaming output
      "#o0" - DISABLE continuous streaming output. Also see #f below.
      "#o1" - ENABLE continuous streaming output.
      
      // Angles output
      "#ob" - Output angles in BINARY format (yaw/pitch/roll as binary float, so one output frame
              is 3x4 = 12 bytes long).
      "#ot" - Output angles in TEXT format (Output frames have form like "#YPR=-142.28,-5.38,33.52",
              followed by carriage return and line feed [\r\n]).
      "#ox" - Output angles and linear acceleration and rotational
              velocity. Angles are in degrees, acceleration is
              in units of 1.0 = 1/256 G (9.8/256 m/s^2). Rotational
              velocity is in rad/s. (Output frames have form like
              "#YPRAG=-142.28,-5.38,33.52,0.1,0.1,1.0,0.01,0.01,0.01",
              followed by carriage return and line feed [\r\n]).
     
      // Sensor calibration
      "#oc" - Go to CALIBRATION output mode.
      "#on" - When in calibration mode, go on to calibrate NEXT sensor.
      
      // Sensor data output
      "#osct" - Output CALIBRATED SENSOR data of all 9 axes in TEXT format.
                One frame consist of three lines - one for each sensor: acc, mag, gyr.
      "#osrt" - Output RAW SENSOR data of all 9 axes in TEXT format.
                One frame consist of three lines - one for each sensor: acc, mag, gyr.
      "#osbt" - Output BOTH raw and calibrated SENSOR data of all 9 axes in TEXT format.
                One frame consist of six lines - like #osrt and #osct combined (first RAW, then CALIBRATED).
                NOTE: This is a lot of number-to-text conversion work for the little 8MHz chip on the Razor boards.
                In fact it's too much and an output frame rate of 50Hz can not be maintained. #osbb.
      "#oscb" - Output CALIBRATED SENSOR data of all 9 axes in BINARY format.
                One frame consist of three 3x3 float values = 36 bytes. Order is: acc x/y/z, mag x/y/z, gyr x/y/z.
      "#osrb" - Output RAW SENSOR data of all 9 axes in BINARY format.
                One frame consist of three 3x3 float values = 36 bytes. Order is: acc x/y/z, mag x/y/z, gyr x/y/z.
      "#osbb" - Output BOTH raw and calibrated SENSOR data of all 9 axes in BINARY format.
                One frame consist of 2x36 = 72 bytes - like #osrb and #oscb combined (first RAW, then CALIBRATED).
      
      // Error message output        
      "#oe0" - Disable ERROR message output.
      "#oe1" - Enable ERROR message output.
      "#oec" - Output ERROR COUNT.
      "#oem" - Output MATH ERROR COUNT.


  "#I" - Toggle INERTIAL-only mode for yaw computation.


  "#f" - Request one output frame - useful when continuous output is disabled and updates are
         required in larger intervals only. Though #f only requests one reply, replies are still
         bound to the internal 20ms (50Hz) time raster. So worst case delay that #f can add is 19.99ms.
 
  
  "#s<xy>" - Request synch token - useful to find out where the frame boundaries are in a continuous
         binary stream or to see if tracker is present and answering. The tracker will send
         "#SYNCH<xy>\r\n" in response (so it's possible to read using a readLine() function).
         x and y are two mandatory but arbitrary bytes that can be used to find out which request
         the answer belongs to.


  ("#C" and "#D" - Reserved for communication with optional Bluetooth module.)
  
  Newline characters are not required. So you could send "#ob#o1#s", which
  would set binary output mode, enable continuous streaming output and request
  a synch token all at once.
  
  The status LED will be on if streaming output is enabled and off otherwise.
  
  Byte order of binary output is little-endian: least significant byte comes first.
*/



/*****************************************************************/
/*********** USER SETUP AREA! Set your options here! *************/
/*****************************************************************/

// HARDWARE OPTIONS
/*****************************************************************/
// Select your hardware here by uncommenting one line!
//#define HW__VERSION_CODE 10125 // SparkFun "9DOF Razor IMU" version "SEN-10125" (HMC5843 magnetometer)
#define HW__VERSION_CODE 10736 // SparkFun "9DOF Razor IMU" version "SEN-10736" (HMC5883L magnetometer) //qmc5883 magnetometer
//#define HW__VERSION_CODE 14001 // SparkFun "9DoF Razor IMU M0" version "SEN-14001"
//#define HW__VERSION_CODE 10183 // SparkFun "9DOF Sensor Stick" version "SEN-10183" (HMC5843 magnetometer)
//#define HW__VERSION_CODE 10321 // SparkFun "9DOF Sensor Stick" version "SEN-10321" (HMC5843 magnetometer)
//#define HW__VERSION_CODE 10724 // SparkFun "9DOF Sensor Stick" version "SEN-10724" (HMC5883L magnetometer)


// OUTPUT OPTIONS
/*****************************************************************/
// Set your serial port baud rate used to send out data here!
#define OUTPUT__BAUD_RATE 57600
#if HW__VERSION_CODE == 14001
// Set your port used to send out data here!
#define LOG_PORT SERIAL_PORT_USBVIRTUAL
#else
// Set your port used to send out data here!
#define LOG_PORT Serial
#endif // HW__VERSION_CODE

// Sensor data output interval in milliseconds
// This may not work, if faster than 20ms (=50Hz)
// Code is tuned for 20ms, so better leave it like that
#define OUTPUT__DATA_INTERVAL 20  // in milliseconds

// Output mode definitions (do not change)
#define OUTPUT__MODE_CALIBRATE_SENSORS 0 // Outputs sensor min/max values as text for manual calibration
#define OUTPUT__MODE_ANGLES 1 // Outputs yaw/pitch/roll in degrees
#define OUTPUT__MODE_SENSORS_CALIB 2 // Outputs calibrated sensor values for all 9 axes
#define OUTPUT__MODE_SENSORS_RAW 3 // Outputs raw (uncalibrated) sensor values for all 9 axes
#define OUTPUT__MODE_SENSORS_BOTH 4 // Outputs calibrated AND raw sensor values for all 9 axes
#define OUTPUT__MODE_ANGLES_AG_SENSORS 5 // Outputs yaw/pitch/roll in degrees + linear accel + rot. vel
// Output format definitions (do not change)
#define OUTPUT__FORMAT_TEXT 0 // Outputs data as text
#define OUTPUT__FORMAT_BINARY 1 // Outputs data as binary float

// Select your startup output mode and format here!
int output_mode = OUTPUT__MODE_ANGLES;
int output_format = OUTPUT__FORMAT_TEXT;

// Select if serial continuous streaming output is enabled per default on startup.
#define OUTPUT__STARTUP_STREAM_ON true  // true or false

// If set true, an error message will be output if we fail to read sensor data.
// Message format: "!ERR: reading <sensor>", followed by "\r\n".
boolean output_errors = false;  // true or false

// Bluetooth
// You can set this to true, if you have a Rovering Networks Bluetooth Module attached.
// The connect/disconnect message prefix of the module has to be set to "#".
// (Refer to manual, it can be set like this: SO,#)
// When using this, streaming output will only be enabled as long as we're connected. That way
// receiver and sender are synchronzed easily just by connecting/disconnecting.
// It is not necessary to set this! It just makes life easier when writing code for
// the receiving side. The Processing test sketch also works without setting this.
// NOTE: When using this, OUTPUT__STARTUP_STREAM_ON has no effect!
#define OUTPUT__HAS_RN_BLUETOOTH false  // true or false
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
void loop()
{
  // Read incoming control messages
 #if HW__VERSION_CODE == 14001
  // Compatibility fix : if bytes are sent 1 by 1 without being read, available() might never return more than 1...
  // Therefore, we need to read bytes 1 by 1 and the command byte needs to be a blocking read...
  if (LOG_PORT.available() >= 1)
  {
    if (LOG_PORT.read() == '#') // Start of new control message
    {
      int command = readChar(); // Commands
#else
  if (LOG_PORT.available() >= 2)
  {
    if (LOG_PORT.read() == '#') // Start of new control message
    {
      int command = LOG_PORT.read(); // Commands
#endif // HW__VERSION_CODE
      if (command == 'f') // request one output _f_rame
        output_single_on = true;
      else if (command == 's') // _s_ynch request
      {
        // Read ID
        byte id[2];
        id[0] = readChar();
        id[1] = readChar();
        
        // Reply with synch message
        LOG_PORT.print("#SYNCH");
        LOG_PORT.write(id, 2);
        LOG_PORT.println();
      }
      else if (command == 'o') // Set _o_utput mode
      {
        char output_param = readChar();
        if (output_param == 'n')  // Calibrate _n_ext sensor
        {
          curr_calibration_sensor = (curr_calibration_sensor + 1) % 3;
          reset_calibration_session_flag = true;
        }
        else if (output_param == 't') // Output angles as _t_ext
        {
          output_mode = OUTPUT__MODE_ANGLES;
          output_format = OUTPUT__FORMAT_TEXT;
        }
        else if (output_param == 'b') // Output angles in _b_inary format
        {
          output_mode = OUTPUT__MODE_ANGLES;
          output_format = OUTPUT__FORMAT_BINARY;
        }
        else if (output_param == 'c') // Go to _c_alibration mode
        {
          output_mode = OUTPUT__MODE_CALIBRATE_SENSORS;
          reset_calibration_session_flag = true;
        }
        else if (output_param == 'x') // Output angles + accel + rot. vel as te_x_t
        {
          output_mode = OUTPUT__MODE_ANGLES_AG_SENSORS;
          output_format = OUTPUT__FORMAT_TEXT;
        }
        else if (output_param == 's') // Output _s_ensor values
        {
          char values_param = readChar();
          char format_param = readChar();
          if (values_param == 'r')  // Output _r_aw sensor values
            output_mode = OUTPUT__MODE_SENSORS_RAW;
          else if (values_param == 'c')  // Output _c_alibrated sensor values
            output_mode = OUTPUT__MODE_SENSORS_CALIB;
          else if (values_param == 'b')  // Output _b_oth sensor values (raw and calibrated)
            output_mode = OUTPUT__MODE_SENSORS_BOTH;

          if (format_param == 't') // Output values as _t_text
            output_format = OUTPUT__FORMAT_TEXT;
          else if (format_param == 'b') // Output values in _b_inary format
            output_format = OUTPUT__FORMAT_BINARY;
        }
        else if (output_param == '0') // Disable continuous streaming output
        {
          turn_output_stream_off();
          reset_calibration_session_flag = true;
        }
        else if (output_param == '1') // Enable continuous streaming output
        {
          reset_calibration_session_flag = true;
          turn_output_stream_on();
        }
        else if (output_param == 'e') // _e_rror output settings
        {
          char error_param = readChar();
          if (error_param == '0') output_errors = false;
          else if (error_param == '1') output_errors = true;
          else if (error_param == 'c') // get error _c_ount
          {
            LOG_PORT.print("#AMG-ERR:");
            LOG_PORT.print(num_accel_errors); LOG_PORT.print(",");
            LOG_PORT.print(num_magn_errors); LOG_PORT.print(",");
            LOG_PORT.println(num_gyro_errors);
          }
          else if (error_param == 'm') // get _m_ath error count
          {
            LOG_PORT.print("#MATH-ERR:");
            LOG_PORT.println(num_math_errors);
          }
        }
      }
      else if (command == 'p') // Set _p_rint calibration values
      {
         LOG_PORT.print("ACCEL_X_MIN:");LOG_PORT.println(ACCEL_X_MIN);
         LOG_PORT.print("ACCEL_X_MAX:");LOG_PORT.println(ACCEL_X_MAX);
         LOG_PORT.print("ACCEL_Y_MIN:");LOG_PORT.println(ACCEL_Y_MIN);
         LOG_PORT.print("ACCEL_Y_MAX:");LOG_PORT.println(ACCEL_Y_MAX);
         LOG_PORT.print("ACCEL_Z_MIN:");LOG_PORT.println(ACCEL_Z_MIN);
         LOG_PORT.print("ACCEL_Z_MAX:");LOG_PORT.println(ACCEL_Z_MAX);
         LOG_PORT.println(""); 
         LOG_PORT.print("MAGN_X_MIN:");LOG_PORT.println(MAGN_X_MIN);
         LOG_PORT.print("MAGN_X_MAX:");LOG_PORT.println(MAGN_X_MAX);
         LOG_PORT.print("MAGN_Y_MIN:");LOG_PORT.println(MAGN_Y_MIN);
         LOG_PORT.print("MAGN_Y_MAX:");LOG_PORT.println(MAGN_Y_MAX);
         LOG_PORT.print("MAGN_Z_MIN:");LOG_PORT.println(MAGN_Z_MIN);
         LOG_PORT.print("MAGN_Z_MAX:");LOG_PORT.println(MAGN_Z_MAX);
         LOG_PORT.println("");
         LOG_PORT.print("MAGN_USE_EXTENDED:");
         if (CALIBRATION__MAGN_USE_EXTENDED) 
           LOG_PORT.println("true");
         else
           LOG_PORT.println("false");
         LOG_PORT.print("magn_ellipsoid_center:[");LOG_PORT.print(magn_ellipsoid_center[0],4);LOG_PORT.print(",");
         LOG_PORT.print(magn_ellipsoid_center[1],4);LOG_PORT.print(",");
         LOG_PORT.print(magn_ellipsoid_center[2],4);LOG_PORT.println("]");
         LOG_PORT.print("magn_ellipsoid_transform:[");
         for(int i = 0; i < 3; i++){
           LOG_PORT.print("[");
           for(int j = 0; j < 3; j++){
             LOG_PORT.print(magn_ellipsoid_transform[i][j],7);
             if (j < 2) LOG_PORT.print(",");
           }
           LOG_PORT.print("]");
           if (i < 2) LOG_PORT.print(",");
         }
         LOG_PORT.println("]");
         LOG_PORT.println(""); 
         LOG_PORT.print("GYRO_AVERAGE_OFFSET_X:");LOG_PORT.println(GYRO_AVERAGE_OFFSET_X);
         LOG_PORT.print("GYRO_AVERAGE_OFFSET_Y:");LOG_PORT.println(GYRO_AVERAGE_OFFSET_Y);
         LOG_PORT.print("GYRO_AVERAGE_OFFSET_Z:");LOG_PORT.println(GYRO_AVERAGE_OFFSET_Z);
      }
	  else if (command == 'c') // Set _i_nput mode
      {
        char input_param = readChar();
        if (input_param == 'a')  // Calibrate _a_ccelerometer
        {
          char axis_param = readChar();
          char type_param = readChar();
          float value_param = LOG_PORT.parseFloat();
          if (axis_param == 'x')  // x value
          {
            if (type_param == 'm')
              ACCEL_X_MIN = value_param;
            else if (type_param == 'M')
              ACCEL_X_MAX = value_param;
          }
          else if (axis_param == 'y')  // y value
          {
            if (type_param == 'm')
              ACCEL_Y_MIN = value_param;
            else if (type_param == 'M')
              ACCEL_Y_MAX = value_param;
          }
          else if (axis_param == 'z')  // z value
          {
            if (type_param == 'm')
              ACCEL_Z_MIN = value_param;
            else if (type_param == 'M')
              ACCEL_Z_MAX = value_param;
          }
          recalculateAccelCalibration();
        }
        else if (input_param == 'm')  // Calibrate _m_agnetometer (basic)
        {
          //disable extended magnetometer calibration
          CALIBRATION__MAGN_USE_EXTENDED = false;
          char axis_param = readChar();
          char type_param = readChar();
          float value_param = LOG_PORT.parseFloat();
          if (axis_param == 'x')  // x value
          {
            if (type_param == 'm')
              MAGN_X_MIN = value_param;
            else if (type_param == 'M')
              MAGN_X_MAX = value_param;
          }
          else if (axis_param == 'y')  // y value
          {
            if (type_param == 'm')
              MAGN_Y_MIN = value_param;
            else if (type_param == 'M')
              MAGN_Y_MAX = value_param;
          }
          else if (axis_param == 'z')  // z value
          {
            if (type_param == 'm')
              MAGN_Z_MIN = value_param;
            else if (type_param == 'M')
              MAGN_Z_MAX = value_param;
          }
          recalculateMagnCalibration();
        }
        else if (input_param == 'c')  // Calibrate magnetometerellipsoid_c_enter (extended)
        {
          //enable extended magnetometer calibration
          CALIBRATION__MAGN_USE_EXTENDED = true;
          char axis_param = readChar();
          float value_param = LOG_PORT.parseFloat();
          if (axis_param == 'x')  // x value
              magn_ellipsoid_center[0] = value_param;
          else if (axis_param == 'y')  // y value
              magn_ellipsoid_center[1] = value_param;
          else if (axis_param == 'z')  // z value
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

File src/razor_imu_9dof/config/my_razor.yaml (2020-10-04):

## USB port
port: /dev/ttyUSB0


##### Calibration ####
### accelerometer
accel_x_min: -308.0
accel_x_max: 225.0
accel_y_min: -317.0
accel_y_max: 376.0
accel_z_min: -309.0
accel_z_max: 431.0

### magnetometer
# standard calibration
magn_x_min: -3803.0
magn_x_max: 753.0
magn_y_min: -3065.0
magn_y_max: 1622.0
magn_z_min: -4426.0
magn_z_max: 1120.0

# extended calibration
calibration_magn_use_extended: false
magn_ellipsoid_center: [92.9121, 35.0553, 207.312]
magn_ellipsoid_transform: [[92.9121, 35.0553, 207.312], [92.9121, 35.0553, 207.312], [92.9121, 35.0553, 207.312]]

# AHRS to robot calibration
imu_yaw_calibration: 0.0

### gyroscope
gyro_average_offset_x: -6.40
gyro_average_offset_y: 35.97
gyro_average_offset_z: 17.23

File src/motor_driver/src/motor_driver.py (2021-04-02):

#!/usr/bin/env python3


import time
import sys
from time import sleep
import RPi.GPIO as GPIO
import rospy
from geometry_msgs.msg import Twist
import math
import pigpio

class Motor_Driver:
    CW = 1
    CCW = 0

    SPR = 200   # Steps per Revolution (360 / 1.8)    
    PI = 3.14159265359
    wheel_radius = 0.074 / 2 #0.037
    wheelSep = 0.288
    DIST_PER_RAD = 2 * PI * wheel_radius        #0.232477856

    def __init__(self, dir1, step1, en1, dir2, step2, en2):
        self.DIR1 = dir1
        self.STEP1 = step1
        self.DIR2 = dir2
        self.STEP2 = step2
        self.EN1 = en1
        self.EN2 = en2
        self.prev_rpm_left = 0
        self.prev_rpm_right = 0
        
        GPIO.setmode(GPIO.BCM)
        GPIO.setup(self.DIR1, GPIO.OUT)
        GPIO.setup(self.STEP1, GPIO.OUT)

        GPIO.setup(self.EN1, GPIO.OUT)
        GPIO.setup(self.EN2, GPIO.OUT)

        GPIO.output(self.EN1, GPIO.HIGH)
        GPIO.output(self.EN2, GPIO.HIGH)
        rospy.loginfo("Disabled drivers, speed 0!")

        GPIO.setmode(GPIO.BCM)
        GPIO.setup(self.DIR2, GPIO.OUT)
        GPIO.setup(self.STEP2, GPIO.OUT)
        self.pi = pigpio.pi()
        self.real_cmd_vel_pub = rospy.Publisher("/ppp/real_cmd_vel", Twist, queue_size = 500)        


    def run(self, rpm_left, rpm_right):
        move_cmd = Twist()

        if rpm_left == 0 and rpm_right == 0:
            if(self.prev_rpm_left != rpm_left and self.prev_rpm_right != rpm_right):
                # rospy.loginfo("Disabled drivers, speed 0!")
                GPIO.output(self.EN1, GPIO.HIGH)
                GPIO.output(self.EN2, GPIO.HIGH)
                self.prev_rpm_left = rpm_left
                self.prev_rpm_right = rpm_right
                move_cmd.angular.z = 0
                move_cmd.linear.x = 0

                self.real_cmd_vel_pub.publish(move_cmd)
            return
        else:
            if(self.prev_rpm_left != rpm_left and self.prev_rpm_right != rpm_right):
                # rospy.loginfo("Enabled drivers, rpm "+str(rpm_left))
                GPIO.output(self.EN1, GPIO.LOW)
                GPIO.output(self.EN2, GPIO.LOW)

        self.prev_rpm_left = rpm_left
        self.prev_rpm_right = rpm_right
        
        start = time.time()
        left_w = rpm_left < 0
        right_w = rpm_right < 0

        #https://www.se.com/no/en/faqs/FA337686/
        # fz = RPM / ((a/360)*60)

        fz_left = (rpm_left * 60) / 0.3
        fz_right = (rpm_right * 60) / 0.3

        self.pi.set_PWM_dutycycle(self.STEP1, 255)  # PWM 1/2 On 1/2 Off
        self.pi.set_PWM_frequency(self.STEP1, abs(fz_left))  # 500 pulses per second
        
        self.pi.set_PWM_dutycycle(self.STEP2, 255)  # PWM 1/2 On 1/2 Off
        self.pi.set_PWM_frequency(self.STEP2, abs(fz_right))  # 500 pulses per second
        
        self.pi.write(self.DIR1, left_w if self.CW else self.CCW)  # Set direction
        self.pi.write(self.DIR2, right_w if self.CW else self.CCW)  # Set direction
        
        #----------------------------------------------

        real_fz_left = self.pi.get_PWM_frequency(self.STEP1)
        real_fz_right = self.pi.get_PWM_frequency(self.STEP2)

        real_fz_left = real_fz_left * math.copysign(1, fz_left)
        real_fz_right = real_fz_right * math.copysign(1, fz_right)
        
        real_rpm_left = (real_fz_left * 0.3) / 60
        real_rpm_right = (real_fz_right * 0.3) / 60

        real_velocity_left = real_rpm_left * self.DIST_PER_RAD
        real_velocity_right = real_rpm_right * self.DIST_PER_RAD

        # print("----------------------------")
        # print("real_velocity_left = {}".format(real_velocity_left))
        # print("real_velocity_right = {}".format(real_velocity_right))
        # print("linear_velocity = {}".format((real_velocity_right+real_velocity_left)/2))

        # print("rpm_left = {}".format(rpm_left))
        # print("rpm_right = {}".format(rpm_right))
        # print("----------------------------")
        
        # print("-------------------------------")
        # print("real_velocity_left = {}".format(real_velocity_left))
        # print("real_velocity_right = {}".format(real_velocity_right))
        # print("GET FZ LEFT= {}".format(real_fz_left))
        # print("real_fz_left = {}".format(real_fz_left))
       
        move_cmd.angular.z = (real_velocity_right - real_velocity_left) / self.wheelSep       
        move_cmd.linear.x = (real_velocity_right + real_velocity_left)/2
       
        # print("-------------------------------")
        
        self.real_cmd_vel_pub.publish(move_cmd)

class Driver:
    PI = 3.14159265359
    wheelSep = 0.288
    wheel_radius = 0.074 / 2 #0.037
    DIST_PER_RAD = 2 * PI * wheel_radius       #0.232477856

    def callback(self, msg):
        # rospy.loginfo("Received a /ppp/cmd_vel message!")
        # rospy.loginfo("Linear Components: [%f, %f, %f]" % (
        #     msg.linear.x, msg.linear.y, msg.linear.z))
        # rospy.loginfo("Angular Components: [%f, %f, %f]" % (
        #     msg.angular.x, msg.angular.y, msg.angular.z))
        # if abs(msg.linear.x) > 0 and abs(msg.linear.x) < 0.01 :
        #     msg.linear.x = 0
        #     msg.angular.z = 0
        
        if abs(msg.angular.z) > 0 and abs(msg.angular.z) < 0.08:
            msg.angular.z = 0.08 * math.copysign(1, msg.angular.z) 
       
        if abs(msg.angular.z) > 0.7:
            msg.angular.z = 0.7 * math.copysign(1, msg.angular.z) 
        
        if abs(msg.linear.x) > 0 and abs(msg.linear.x) < 0.01:
            msg.linear.x = 0.01 * math.copysign(1, msg.linear.x) 

        if abs(msg.linear.x) > 0.27:
            msg.linear.x = 0.27 * math.copysign(1, msg.linear.x) 

        l_vel = msg.linear.x - ((self.wheelSep / 2.0) * msg.angular.z)# m/s
        r_vel = msg.linear.x + ((self.wheelSep / 2.0) * msg.angular.z)# m/s

        self._left_rpm = l_vel / self.DIST_PER_RAD
        self._right_rpm = r_vel / self.DIST_PER_RAD

        # print("!!! L SPEED = {}".format(l_vel))
        # print("!!! R SPEED = {}".format(r_vel))
        # print("self._left_rpm  = {}".format(self._left_rpm ))

    def __init__(self):
        rospy.init_node('driver')

        self.motor_driver = Motor_Driver(26, 19, 6,    16, 18, 21)
        
        self._left_rpm = 0
        self._right_rpm = 0

        self._timeout = rospy.get_param('~timeout', 2)
        self._rate = rospy.get_param('~rate', 1000)

        self.ros_sub_twist = rospy.Subscriber("/ppp/cmd_vel", Twist, self.callback)
        rospy.loginfo("Initialization complete")

    def run(self):

        rate = rospy.Rate(self._rate)

        while not rospy.is_shutdown():
            self.motor_driver.run(self._left_rpm, self._right_rpm)
            rate.sleep()
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

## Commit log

2020-09-17 Add files via upload
    add urdf
    [12GAN20__1__1.stl, 12GAN20__1__Mirror__1.stl, 18650 (1) (1).stl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]
2020-09-18 Add files via upload
    add ultrasonyc sersors for arduino
2020-09-18 Add files via upload
    add sensors
    [ppp.xacro]
2020-09-20 Add files via upload
    add subscriber for fan and two brushes
2020-09-20 Add files via upload
    new urdf
2020-09-20 Add files via upload
    Fix all for simulate
    [controller.yaml, ppp.xacro]
2020-10-04 new file: brushUltraSonycSensorsVoltage/CMakeLists.txt new file: brushUltraSonycSensorsVoltage/launch/brush-ultrasonyc-sensors-voltage.launch new file: brushUltraSonycSensorsVoltage/package.xml new f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
2020-10-04 deleted: 3_2.ino deleted: ppp.gazebo deleted: ppp.xacro new file: razor_imu_9dof/.gitignore new file: razor_imu_9dof/.vscode/c_cpp_properties.json new file: razor_imu_9dof/.vscode/settings.json new f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
    [imu.cfg, ppp.xacro]
2020-10-04 deleted: razor_imu_9dof/.gitignore deleted: razor_imu_9dof/.vscode/c_cpp_properties.json deleted: razor_imu_9dof/.vscode/settings.json deleted: razor_imu_9dof/CHANGELOG.rst deleted: razor_imu_9dof/CM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
    [12GAN20__1__1.stl, 12GAN20__1__Mirror__1.stl, 18650 (1) (1).stl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]
2020-10-04 renamed: src/brushUltraSonycSensorsVoltage/src/3_2.ino -> src/brushUltraSonycSensorsVoltage/src/3_2/3_2.ino new file: src/motor_driver/launch/motor-driver.launch modified: src/motor_driver/src/motor_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
2020-10-06 fix project v1
    [imu.cfg]
2020-10-07 add v1 odometry pub node
2020-10-11 fix range sensors & change usb port
2020-10-12 add lidar
    [Component35_1.stl, Component36_1.stl, Component37_1.stl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]
2020-10-12 add gazebo ref to lidar
2020-10-22 add hw & new motor control
2020-10-22 fix lidar
    [ppp.xacro]
2020-10-23 set wheel independant
2020-10-23 v1 hw & v1 for load controller
    [controller.yaml]
2020-10-26 add launch & del comments
    [controller.yaml]
2020-10-27 add diff drive
    [ppp.xacro]
2020-11-13 add razor imu
    [imu.cfg]
2020-11-13 rename imu
    [imu.cfg]
2020-11-14 change ppp position yaw & change mapping launch
    [ppp.xacro]
2020-11-15 fix launch hector
    [ppp.xacro]
2020-11-15 add new urdf turned -90
    [12GAN20__1__1.stl, 12GAN20__1__Mirror__1.stl, 18650 (1) (1).stl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]
2020-11-17 add correct urdf & debug settings & tf
    [12GAN20__1__1.stl, 12GAN20__1__Mirror__1.stl, 18650 (1) (1).stl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]
2020-11-20 fix odom
    [ppp.xacro, ppp90.xacro]
2020-11-28 add some conf
    [ppp90.xacro]
2020-11-28 add localization config
    [ppp90.xacro]
2020-12-02 fix model direction
    [ppp90.xacro]
2020-12-05 fix v1 acml
    [ppp90.xacro]
2020-12-06 add range sensors to point cloud
2020-12-18 change move base
    [ppp90.xacro]
2020-12-19 fix emulation & controllers
    [controller.yaml, ppp90.xacro]
2020-12-20 v1 fix urdf
    [Forward_wheel.stl, fw_wheel_1.stl, fww_a_1.stl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]
2020-12-20 turn model
    [12GAN20__1__1.stl, 12GAN20__1__Mirror__1.stl, Component35_1.stl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]
2020-12-22 ebaniy urdf
    [ppp.xacro, ppp90.xacro]
2020-12-24 fix some params
    [ppp90.xacro]
2020-12-26 50/50 gazebo
    [controller.yaml, ppp90.xacro]
2020-12-26 gazebo ok 2/3
    [controller.yaml]
2020-12-29 fix sonic position
    [ppp90.xacro]
2020-12-30 roll back motor_driver
2021-01-01 fix gazebo OK!!!
    [controller.yaml, ppp90.xacro]
2021-01-06 test ball, in progress
    [controller.yaml, ppp90.xacro]
2021-01-11 wheelSep ok!!!
2021-01-13 cmd add wheel different rpm
2021-01-13 urdf caster wheel ok
    [ppp90.xacro]
2021-01-13 urdf ok
    [ppp90.xacro]
2021-01-14 remove imu
2021-01-15 turn lidar
    [ppp90.xacro]
2021-01-15 fucking urdf
    [ppp90.xacro]
2021-01-15 change setp2 pin to 19
2021-01-17 change wheel sep
2021-01-17 disable log in odom & fix cmdVel if chaged when processes
    [motor_driver.py]
2021-02-01 add circle footprint
